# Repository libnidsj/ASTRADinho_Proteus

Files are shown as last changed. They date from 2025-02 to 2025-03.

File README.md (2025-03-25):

# Proteus Astra G 2.0 (Bosch M1.5.5 PnP)

# Acerto

## Alvo de Lenta

## Alvos de Lambda

## Alvos de Temperatura

## Pops

## Launch Control

## Demais funções a implementar

## Sujestões de moficações mecânicas

- Injetor de partida a frio

# Observações

## Atuador de Lenta

Atuador de lenta original funciona como um motor de passo DC, operado por ponte H. Testada a implementação do mesmo, porém o veículo mantém a mesma característica da I.E. original, com o controle de lenta sendo bastante deficiente e a rotação de marcha lenta oscilando. Além disso, foi notado que o atuador perde calibração após certo tempo de uso, sendo instável a razão de queda para lenta.

Foi optado por adaptar um atuador de lenta do tipo dupla solenóide, com código **0280140553**, utilizando um suporte impresso em 3D (Arquivo .STL salvo no repositório, impresso em ABS). Na parte elétrica, foi mantido o conector do atuador de lenta original, porém adicionado um conector extra para o novo.

**Limitações da implementação:** Por utilizar a entrada do coletor original da PCV, a mesma necessitou ser isolada, sendo necessário futuramente a adaptação de uma catch CAN.

## Temperatura e Ventoinhas

No veículo em si, há uma discrepância entre as documentações e os pinos da central original. Por se tratar de uma unidade com o módulo de arrefecimento, o acionamento das ventoinhas é realizado pelo módulo original, e não pela injeção original.
Para controlar a temperatura de funcionamento, é necessário modular um PWM de 100Hz no pino B06, sendo que 90% de duty equivale a 120 graus, e, 10% de duty a 60-. 

**Diante disso, pela temperatura no painel ser linkada com o acionamento da ventoinha, a mesma pode marcar diferente de antes, mesmo a temperatura real estando mais baixa.** Isto ocorre com a finalidade de acionar a ventoinha precocemente, e, pode ser ajustado caso a ventoinha esteja disparada antes da abertura da válvula termostática.

# Pinout

## Pinout I.E.  Original

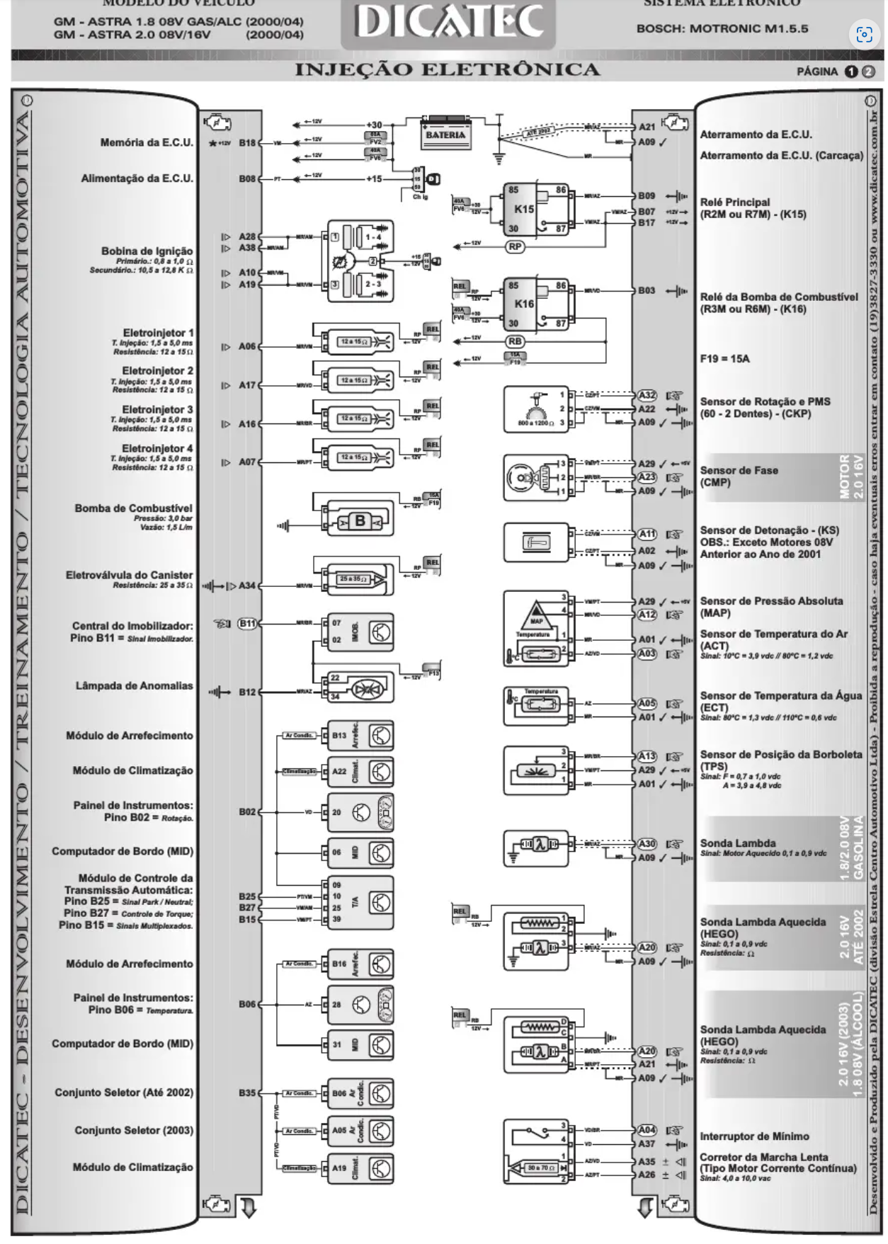
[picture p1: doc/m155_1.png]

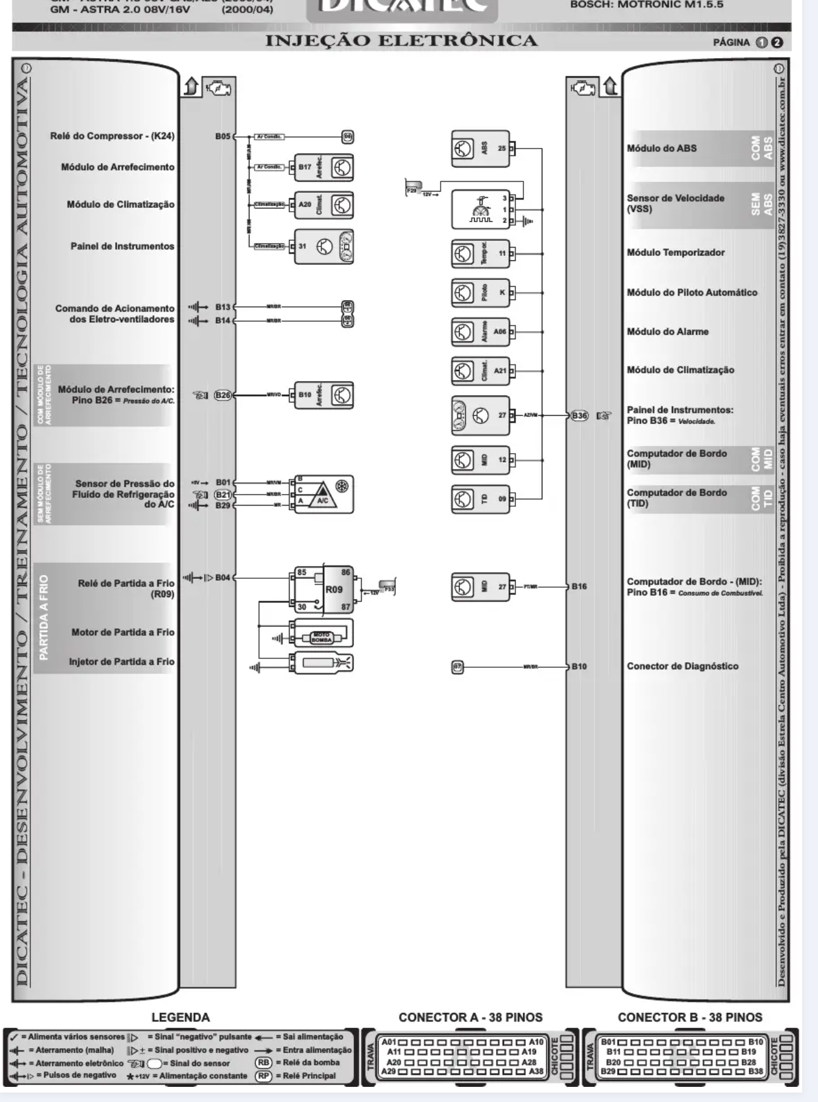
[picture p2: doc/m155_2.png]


## Pinout Proteus

**Black 23**
| Função | Pino Proteus | Pino Bosch |
| - | - | -|
|Fase |1 | - | 
| Velocidade|2 |B36 | 
| DIG3 |3 |- | 
| Rotação 2+|4 |- | 
Rotação 1+|5 |A32 | 
|ETB1-|6 |- | 
|ETB1+|7 |- |
|ETB2-|8 |- |
|DIG5|9 |- |
|DIG1|10 | -|
|DIG6|11 |A04 |
|VR2-|12 |- |
|Rotação 1-|13 |A22 | 
|GND|14 |A09 | 
|ETB2+|15 |- | 
|CAN L|16 | Wide Can L |  
|CAN H|17 | Wide Can H |  
|12V Permanente|18 |B18 |  
|GND|19 | A21|  
|GND|20 | A09|  
|CAN2 L|21 |- |  
|CAN2 H|22 | -|  
|Retorno relé principal|23 | B07 e B17 e A04 |  

**White35**
| Função | Pino Proteus | Pino Bosch | 
| -|- |- |
|Sensor GND | 1 | - |  
|Sensor GND | 2 | A01 |  
|Sensor GND | 3 | B29 |  
|Sensor GND | 4 | B01 |  
|Sensor GND | 5 | - | 
|Sensor GND | 6 | - | 
|Sensor GND | 7 | - | 
|Sensor GND | 8 | - | 
|Sensor 5V | 9 | A29 | 
|Sensor 5V | 10 | -| 
|12V Sensores |11 |- |
|12V Sensores |12 |- |
|MAP |13 |A12 |
|TPS2 |14 |- |
|12V +15 |15 | B08| 
|PPS2 |16 | -|
|Sinal Ventoinha |17 | B13|
|Sinal Ar |18 |B35 |
|Temp 1 |19 | -|
|ECT |20 |A05 |
|Sensor 5V |21 | -|
|Sensor 5V | 22| -|
|Sensor GND | 23| -|
|TPS |24 |A13 |
|Sinal Ar 1 |25 | B26| 
|Sinal Ar 2 |26 | B21|
|Analog Volt 8 |27 | -|
|Analog Volt 10 |28 |- |
|Sensor GND |29 |- |
|IAT |30 | A03|
|Temp 4 |31 |- | 
|5V Sensor |32 | -| 
|5V Sensor |33 |- | 
|Knock 1 |34 | -| 
|Knock 2 |35 |- | 

BLACK35
| Função | Pino Proteus | Pino Bosch | 
| -|- |- |
| High 2| 1| -|
| High 1| 2| -|
| Inj 1|3 | A06|
| Inj 3|4| A16 |
| Luz injeção | 5 | B12 |
| Rotação Painel | 6 | B02 |
| Relé compressor | 7 | B05 | 
| Low 11 | 8 | B14 |
| Low 9 | 9 | - |
| At. Lenta 1|10 | A35 |
| At. Lenta 2|11 | A26 |
| Temperatura Painel |12 | B06|
|High 3 |13 |- |
|High 4 |14 |- |
|Inj 2 |15 | A17| 
|Inj 4 |16 | A07|
|PGND |17 |- |
|PGND |18 |- |
|Inj 8 |19 |- |
|Rele Bomba |20 |B03 |
|Rele Principal|21 |B09 |
| Ign 3 |22 | Mod Ign 3 / A10, A19 |
| Low 16 |23 |- |
| PGND |24 | -|
| Ign 12 |25 | -|
| Ign 11 |26 | -|
| Ign 10 |27 | -|
| Ign 9 |28 | -|
| Ign 8 |29 | -|
| Ign 7 |30 | -|
| Ign 6 | 31|- |
| Ign 5 | 32| -|
| Ign 4 | 33| -|
| Ign 2 | 34| -|
| Ign 1 | 35| Mod Ign 1 / A28, A38 |

## Conectores Extras

Foram adicionados três conectores extras ao veículo, dois deles na região da I.E., e, outro na região do atuador de lenta.

- Conector 3 vias região I.E.: 
	- Pino 1: 5V
	- Pino 2: USB D+
	- Pino 3: USB D-
		Observação: Este conector possui um terra em seu chicote, sendo o terra do USB, realizado no local original do aterramento da central eletrônica.

- Conector 2 vias região I.E.:
	- Pino 1: CAN H
	- Pino 2: CAN L
	Observação: Rede CAN construída com o par I.E. + leitor de wideband no painel, formando um rede com impedância de 60ohms.

- Conector 3 vias região do atuador de lenta:
	- Pino 1: Sinal atuador de lenta (1000Hz Low)
	- Pino 2: 12V +15
	- Pino 3: Sinal atuador de lenta (1000Hz Low)

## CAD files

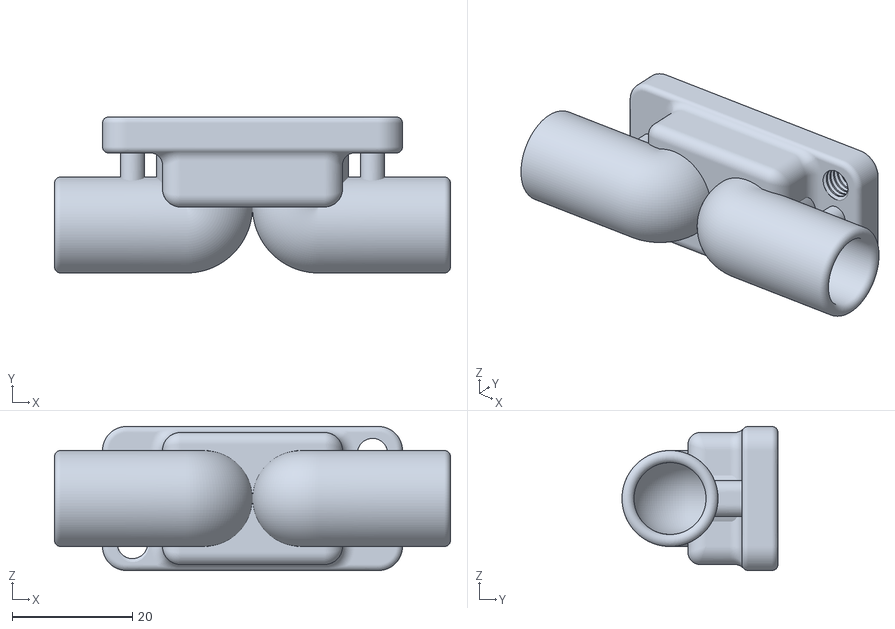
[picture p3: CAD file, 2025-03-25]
Modelos 3D/Suporte_Atuador.stl
66.0 x 26.0 x 24.0

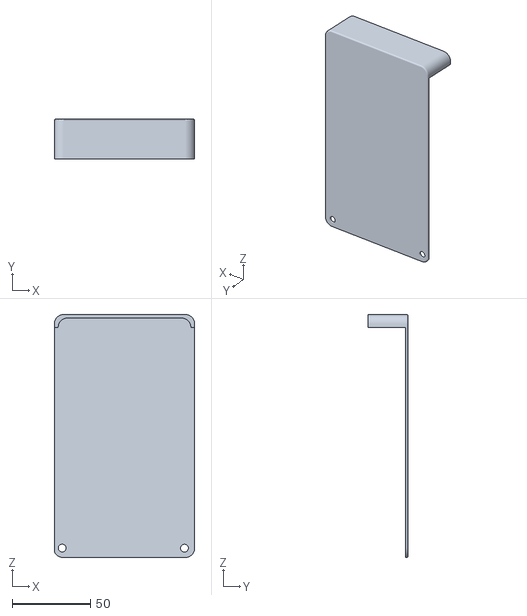
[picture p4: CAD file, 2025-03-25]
Modelos 3D/Tampa IE.stl
89.5 x 25.5 x 155.0

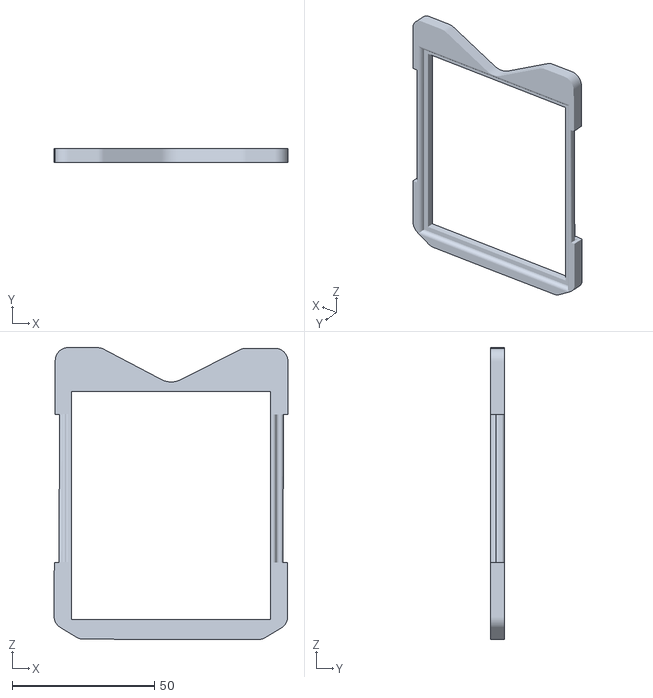
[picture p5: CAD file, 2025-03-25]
Modelos 3D/Suporte Mod Bobinas.stl
82.2 x 5.00 x 102.7

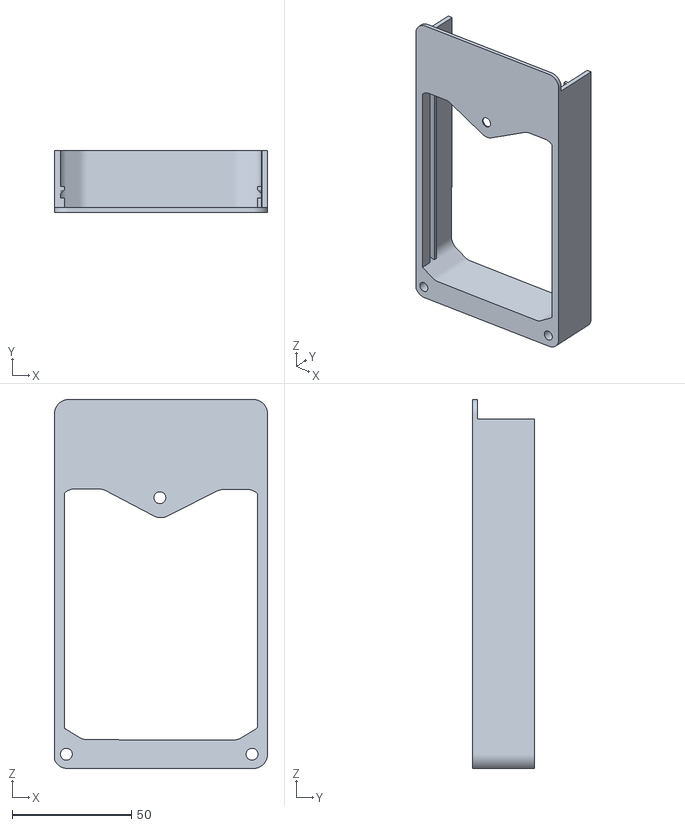
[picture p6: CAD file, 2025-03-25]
Modelos 3D/Corpo IE.stl
89.5 x 26.0 x 155.0
